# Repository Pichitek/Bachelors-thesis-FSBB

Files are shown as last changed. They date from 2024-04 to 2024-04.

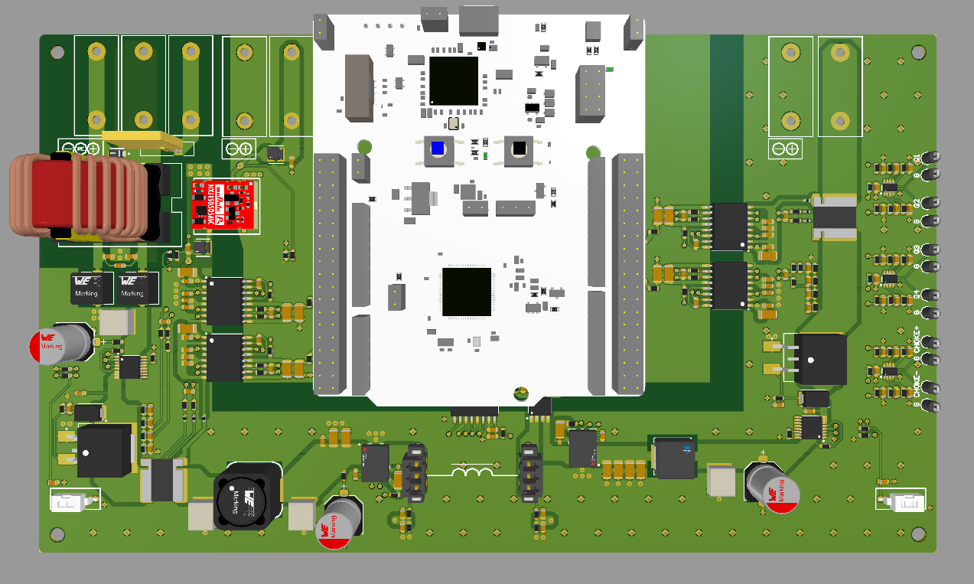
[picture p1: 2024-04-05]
images/altium/pcb_top.png

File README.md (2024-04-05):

# Laboratory model of Four Switch Buck-Boost converter

This project was part of my bachelors thesis at AGH University of Kraków. It contains schematic and PCB design made in Altium Designer 23, simulations of sensing ciruits, filters etc. made in LTSpice, control loop simulation conducted in Simulink and imprementation of control algorithm on STM32G4 microcontroller.

Due to lack of time, this project was finished in its simulation stage, although both schematic and PCB were reviewed by supervisor.

In this repository you can find:
* images folder with all screenshots, plots used while writing thesis
* sch_pcb folder with Altium Designer project
* sim folder with .asc files made in LTSpice
* src folder with control loop simulation, STMCubeIDE project and Jupyter notebook for calculations 
* .pdf's with schematic and thesis (as mentioned, it is written in polish)
* .ppt file which was presented during my defense (also in polish)

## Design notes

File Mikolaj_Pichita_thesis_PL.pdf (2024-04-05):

Akademia Górniczo-Hutnicza im. Stanisława Staszica w Krakowie

WYDZIAŁ INFORMATYKI, ELEKTRONIKI I TELEKOMUNIKACJI

## Projekt dyplomowy

## Model laboratoryjny przetwornicy typu „Buck-Boost” opartej na czterech kluczach tranzystorowych sterowanej cyfrowo Laboratory model of a digitally controlled buck-boost converter based on four transistor switches

Autor: | Mikołaj Pichita
Kierunek studiów: | Elektronika i Telekomunikacja
Opiekun pracy: | dr hab. inż. Cezary Worek, prof. AGH

Kraków, 2024

## Spis treści

SPIS TREŚCI | 3

SPIS TREŚCI | 4

## Wstęp

Przetwornice DC-DC Buck-Boost to uniwersalne urządzenia zapewniające dostarczenie napięcia zasilania z szerokiego zakresu. Łączy ona w sobie funkcjonalności przetwornicy Buck oraz Boost. Istnieje wiele różnych topologii dla tego typu przetwornic. Każda z nich posiada swoje zalety, ale również jest obarczona pewnego rodzaju wadami.
Dzięki cyfrowemu sterowaniu taka przetwornica jest w stanie zagwarantować sprawność na bardzo wysokim poziomie oraz stałe napięcie na wyjściu układu. W zaawansowanych systemach do sterowania nie są wykorzystywane powszechnie dostępne na rynku kontrolery. Bardzo często tworzony jest cały system sterowania na dedykowanym procesorze. Zapewnia to elastyczność, której standardowe kontrolery nie są w stanie zagwarantować. Pozwala stworzenie i kalibrację pętli sterowania dokładnie po zaprojektowany układ.

## Cel pracy

Celem pracy jest zaprojektowanie niskonapięciowej przetwornicy DC-DC typu Buck-Boost opartej na czterech kluczach tranzystorowych. Kontrola systemu powinna być zrealizowana poprzez mikrokontroler STM32G474 lub jego płytkę rozwojową. Układ został przygotowany jako model laboratoryjny do celów dydaktycznych.

1. Wprowadzenie do nieizolowanych przetwornic DC-DC | 5

## 1. Wprowadzenie do nieizolowanych przetwornic DC-DC

Niniejszy rozdział ma za zadanie opisać podstawowe funkcjonalności i właściwości nieizolowanych przetwornic DC-DC. Tematem pracy jest opracowanie modelu laboratoryjnego przetwornicy Buck-Boost. Z tego powodu skupiono się na objaśnieniu działania trzech podstawowych trybów działania przetwornicy: Buck, Boost, Buck-Boost oraz objaśnieniu cyfrowego sprzężenia zwrotnego, które zapewnia stabilność całego systemu, filtracji zaburzeń elektromagnetycznych oraz sposobów prowadzenia kluczowych, dla poprawnego działania przetwornicy, sygnałów.

### 1.1. Opis działania przetwornicy typu Buck

Cechą przetwornicy typu Buck jest zapewnienie napięcia wyjściowego układu, które będzie mniejsze od napięcia wejściowego. W najprostszej konfiguracji składa się ona z czterech elementów: elementu kluczującego, najczęściej tranzystora, elementu prostownika, w najprostszym przypadku diody, elementu magazynującego energię w polu magnetycznym oraz elementu filtrującego w postaci kondensatora. [1]

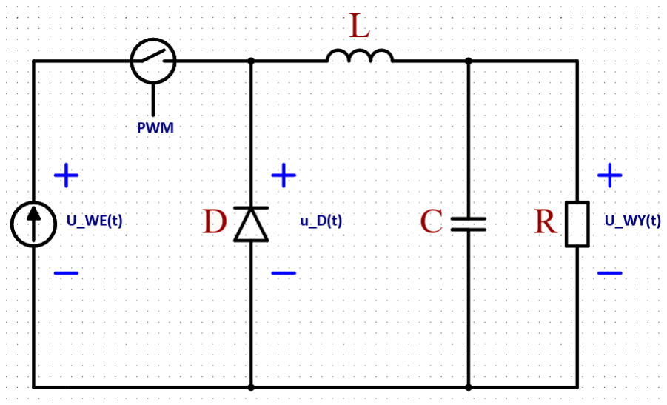
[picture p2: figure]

Rysunek 1. Przetwornica typu Buck

Klucz ma za zadanie obniżyć wartość napięcie wyjściowego przetwornicy poprzez jego włączanie i wyłączanie. Przez to, napięcie na diodzie będzie przypominać falę prostokątną ze współczynnikiem wypełnienia proporcjonalnym do stosunku czasów "włączenia"i "wyłączenia".

D =

tON
tON + tOF F

=

tON
TSW

(1.1)

Gdzie:

– D - współczynnik wypełnienia fali prostokątnej

– tON - czas włączenia tranzystora [s]

– tOF F - czas wyłączenia tranzystora [s]

– TSW - okres trwania jednego cyklu przełączania [s]

1. Wprowadzenie do nieizolowanych przetwornic DC-DC | 6

Aby otrzymać wartość stałą na wyjściu przetwornicy, należy posłużyć się filtrem dolnoprzepustowym. Taki filtr będzie spełniał rolę układu całkującego, tłumiąc składowe wysokoczęstotliwościowe przebiegów, przepuszczając głównie składową stałą przebiegu prostokątnego. W rezultacie można otrzymać wzór opisujący napięcie wyjściowe idealnego konwertera Buck.

VOUT = VIN · D | (1.2)

Gdzie:

– VOUT - napięcie wyjściowe przetwornicy [V]

– VIN - napięcie wejściowe przetwornicy [V]

### 1.2. Opis działania przetwornicy Boost

Przetwornica Boost zwiększa napięcie wyjściowe w stosunku do napięcia wejściowego. Urządzenie wykorzystuje takie same komponenty jak przetwornica Buck, ale zmieniając ich topologię, zapewnia inną funkcjonalność. [1]

Rysunek 2. Przetwornica typu Boost

Gdy klucz jest włączony, napięcie na elemencie indukcyjnym jest równe napięciu wejściowemu, a prąd elementu filtrującego jest równy prądowi obciążenia.

vL = VIN

iC = −

VOUT
R

(1.3)

Gdzie:

– vL - napięcie elementu indukcyjnego [V]

– iC - prąd elementu filtrującego [A]

W czasie, kiedy klucz jest wyłączony, element indukcyjny zmagazynował energię w polu magnetycznym. Ze względu na warunek zachowania ciągłości prądu, powoduje to zmianę napięcia na tym elemencie oraz zmianę prądu przepływającego przez element C.

1. Wprowadzenie do nieizolowanych przetwornic DC-DC | 7

vL = VIN − VOUT

iC = iL −

VOUT
R

(1.4)

Pozwala to wyprowadzić równanie na napięcie wyjściowe przetwornicy:

VOUT = VIN ·

1
1 − D

(1.5)

### 1.3. Opis działania przetwornicy Buck-Boost

Topologia Buck-Boost łączy funkcjonalność obu przetwornic. Taki układ potrafi wyprodukować napięcie wyjściowe, które może być zarówno mniejsze, jak i większe od napięcie wejściowego. Taka elastyczność jest często bardzo przydatna, gdy chcemy wykorzystać tę samą topologię do zasilania urządzeń o różnych napięciach zasilania. [1]

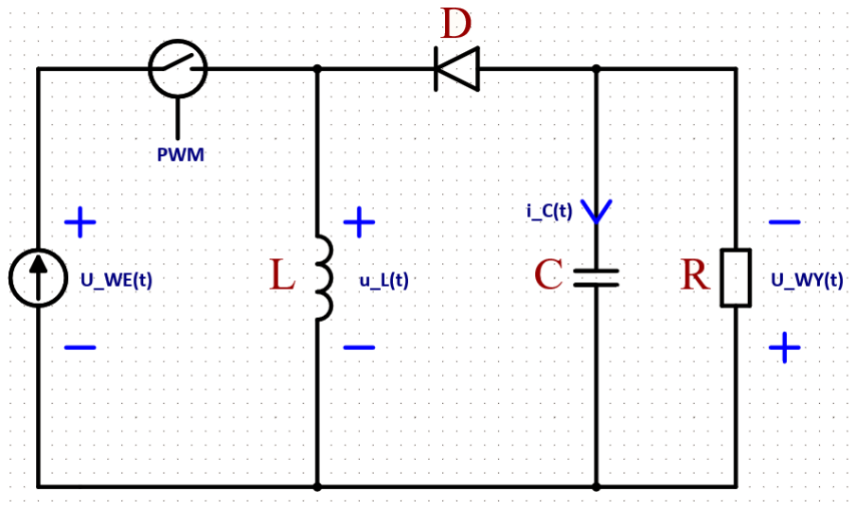
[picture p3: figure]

Rysunek 3. Odwracająca przetwornica typu Buck-Boost

VOUT = VIN ·

D
1 − D

(1.6)

Charakterystycznym elementem tej topologii jest odwrócone napięcie wyjściowe. Aby mogło być ono mierzone względem tego samego potencjału, należy posłużyć się inną topologią przetwornicy Buck-Boost, na przykład topologia SEPIC (single-ended primary-inductor converter) lub topologią opartą na czterech kluczach

tranzystorowych.

1. Wprowadzenie do nieizolowanych przetwornic DC-DC | 8

Rysunek 4. Przetwornica typu Buck-Boost na czterech kluczach

Wprowadzając do modelów przetwornic elementy pasożytnicze m.in. rezystancję szeregową induktora, rezystancję ON klucza, uzyskiwany jest model, który nie jest bezstratny. Parametr sprawności służy do opisywania stosunku mocy wejściowej i mocy wyjściowej przetwornicy, pokazując wpływ strat na jej pracę.

η =

POUT

PIN

(1.7)

Gdzie:

– η - sprawność

– POUT - moc wyjściowa przetwornicy [W]

– PIN - moc wejściowa przetwornicy [W]

### 1.4. Sprzężenie zwrotne przetwornicy DC-DC

Przetwornice impulsowe można opisać jako system składający się z parametrów: napięcia wejściowego UW E, prądu obciążenia (wyjściowego) IW Y i sygnału/ów PWM. Napięcie wyjściowe przetwornicy, będące równocześnie

sygnałem wyjściowym systemu, może być regulowane poprzez zmienianie parametrów wejściowych. Sprzężenia zwrotne w przetwornicach impulsowych są stosowane do zapewnienia stałego, znanego, napięcia wyjściowego. Wykorzystują one sensory prądów i napięć, regulując współczynnik wypełnienia sygnału sterującego klucze. [1]

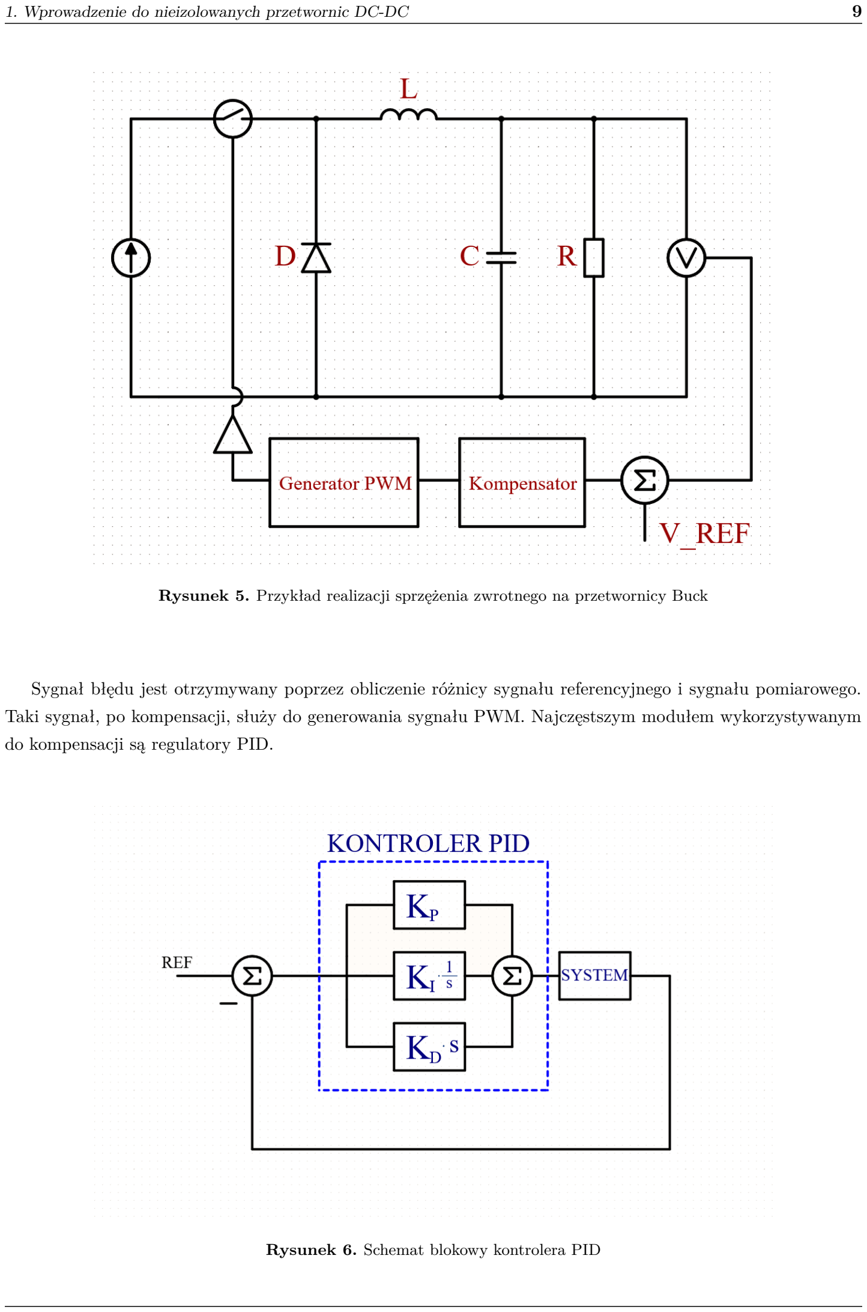
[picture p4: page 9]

1. Wprowadzenie do nieizolowanych przetwornic DC-DC | 9

Rysunek 5. Przykład realizacji sprzężenia zwrotnego na przetwornicy Buck

Sygnał błędu jest otrzymywany poprzez obliczenie różnicy sygnału referencyjnego i sygnału pomiarowego. Taki sygnał, po kompensacji, służy do generowania sygnału PWM. Najczęstszym modułem wykorzystywanym do kompensacji są regulatory PID.

Rysunek 6. Schemat blokowy kontrolera PID

1. Wprowadzenie do nieizolowanych przetwornic DC-DC | 10

Regulator PID (ang. Proportional-Integral-Derivative) jest odpowiedzialny za utrzymywanie stałej wartości

na wyjściu systemu, dynamicznie go regulując, wykorzystując sygnały referencyjne i wyjściowe. Wzmocnienie proporcjonalne KP , ma na celu zapewnienie zbieżności wartości referencyjnej i wyjściowej systemu. Taki regulator, wykorzystujący samo wzmocnienie KP , nie byłby w stanie zapewnić dokładniej zbieżności tych dwóch wartości z powodu błędu stanu ustalonego (ang. steady-state error). Do eliminacji tego błędu służy wzmocnie-

nie KI . Stosując operację całkowania, błąd steady-state, może być znacząco zredukowany, do tego stopnia, że regulatory PI są powszechnie stosowane w systemach sterowania. [8]

Rysunek 7. Typy odpowiedzi regulatora PID, [9]

Wzmocnienie KD, pomaga systemowi w jego tłumieniu, redukując przeregulowanie. Różne dostrojenie wartości KP , KI oraz KD będzie rezultować w różnych odpowiedziach czasowych systemu, minimalizując czas zbieżności lub przeregulowanie.

### 1.5. Filtracja zaburzeń elektromagnetycznych

Zaburzenia elektromagnetyczne to zjawisko objawiające się w powstawaniu zakłóceń w układzie elektronicznym. Wszystkie zakłócenia w systemie są wprowadzane do niego na dwa różne sposoby: poprzez przewodzenie lub poprzez promieniowanie. Oba typy mogą się demonstrować w postaci zakłóceń wspólnych (ang. common-mode) lub różnicowych (ang. differential-mode). Można prosto zdefiniować postaci tych zakłóceń na podstawie

przetwornic DC-DC.

W zasilaczach, naturalnym elementem przebiegów prądu są strome zbocza sygnałów. Takie szybkie zmiany, niosą za sobą dużą zawartość składowych harmonicznych, które mogą zakłócać pracę całego systemu. Taki typ zakłóceń można zdefiniować jako zakłócenia różnicowe. Zakłócenia pojawiają się w systemie na dodatnim biegunie oraz powracają poprzez ujemny biegun. [20]

1. Wprowadzenie do nieizolowanych przetwornic DC-DC | 11

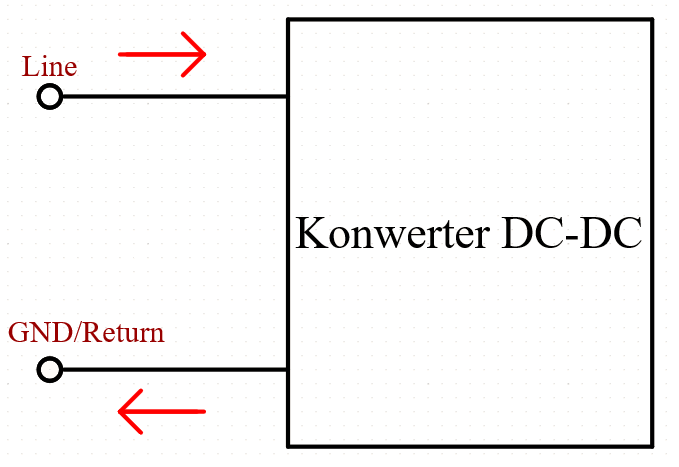
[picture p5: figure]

Rysunek 8. Zobrazowanie zakłóceń różnicowych

Do przedstawienia zakłóceń wspólnych można posłużyć się uproszczeniem. Polega ono na podłączeniu małej pojemności, rzędu kilkunastu pikofaradów, pomiędzy obudową zasilacza a potencjał PE (ang. Protective Earth).

Wszystkie zakłócenia wysokoczęstotliwościowe, nieważne czy pojawią się na biegunie dodatnim czy ujemnym, będą krążyć w systemie, co jest spowodowane sprzężeniem obudowy do PE.

Rysunek 9. Zobrazowanie zakłóceń wspólnych

Do filtracji zakłóceń EMI służą filtry EMI.

1. Wprowadzenie do nieizolowanych przetwornic DC-DC | 12

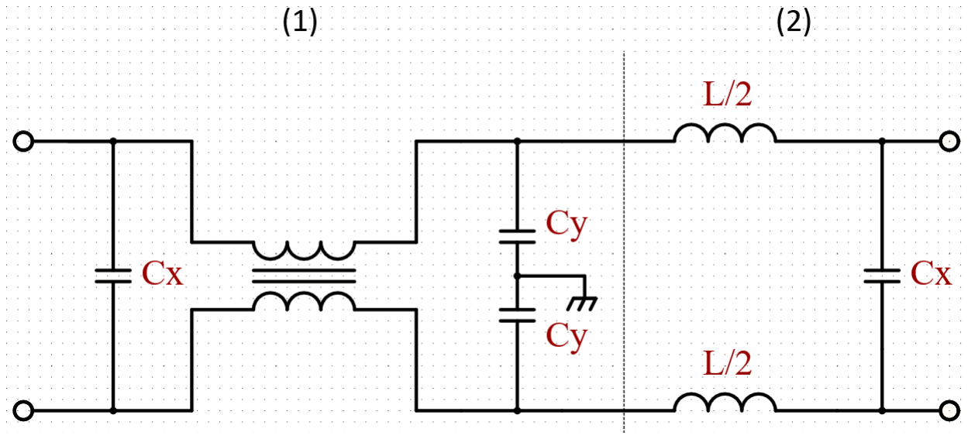
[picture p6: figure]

Rysunek 10. Filtr EMI

Filtr można podzielić na dwie części. Każda z nich jest odpowiedzialna za filtrację innego typu zakłóceń. Część różnicowa (2) to prosty filtr LC, dobrany tak, aby jego częstotliwość odcięcia zapewniała tłumienie zakłóceń powstających poprzez kluczowanie systemu. Część wspólna (1) jest zrealizowana przy pomocy dławika przeciwzakłóceniowego (ang. common-mode choke). Taki dławik, razem z odpowiednio dobranymi kondensato-

rami Cy, pozwala na odfiltrowanie wysokoczęstotliwościowych zakłóceń.
Aby uzyskać zadowalającą odpowiedź impulsową filtru, należy zadbać o jego poprawne tłumienie (ang damping). Damping zapewnia wyeliminowanie rezonansów pomiędzy elementami magnetycznymi a pojemnościo-

wymi, objawiających się w charakterystykach AC. Proces tłumienia polega na wprowadzeniu równolegle do układu dodatkowej gałęzi z pojemnością Cd oraz rezystancją Rd. Dobrym założeniem jest, aby wartość pojemności w gałęzi odpowiadającej za tłumienie, była od 5 do 10 razy większa od pojemności Cx. Aby zapewnić tłumienie krytyczne należy zadbać, aby dobroć układu była równa 1. [17]

Q =

1
R

·

r
L
C

(1.8)

Dzięki takiemu założeniu i wzorze [1.8] można poznać wartość rezystancji Rd.

Rd =

r
L
Cx | (1.9)

### 1.6. Techniki separacji i izolacji sygnałów w przetwornicach impulsowych

Częstą praktyką w przetwornicach DC-DC jest izolowanie toru mocy od części układu odpowiedzialnego za sterowanie. Jakość izolacji można podzielić na cztery klasy:

– izolacja funkcjonalna - najprostszy i najtańszy typ izolacji, w transformatorze izolującym nie występuje żadna warstwa izolująca jego uzwojenia, nie zapewnia ochrony przed porażeniem elektrycznym, służy głównie do przerywania na płycie PCB dużych pętli masy

– izolacja podstawowa - zapewnia ochronę przed porażeniem pod warunkiem, że warstwa materiału izolującego uzwojenia transformatora pozostała nienaruszona

– izolacja wspomagająca - porównując do izolacji podstawowej, dodawana jest kolejna warstwa materiału izolującego

1. Wprowadzenie do nieizolowanych przetwornic DC-DC | 13

– izolacja wzmocniona - oprócz izolacji uzwojeń, ten typ izolacji wymaga zachowania odpowiedniej odległości od elementów przewodzących

Problemem, z którym mierzą się przetwornice DC-DC, są zakłócenia pojawiające się na poligonie masy. Najprostszym sposobem na ochronę ważnych sygnałów, sterujących bramki tranzystorów, czy pomiarów prądu, napięcia, temperatury, jest zastosowanie pewnego rodzaju izolacji. Dzieląc potencjały odniesienia, redukowana jest szansa na zakłócenie sygnału wymaganego do pracy układu. [19]

2. Projekt przetwornicy | 14

## 2. Projekt przetwornicy

W poniższym rozdziale zostanie szczegółowo omówiony proces projektowania przetwornicy Buck-Boost. Zostaną zaprezentowane bloki funkcjonalne przetwornicy, fragmenty schematu, uzasadnienia wyboru komponentów, a na sam koniec omówiony zostanie projekt PCB. Schematy i płytkę PCB zaprojektowano korzystając z programu Altium Designer.

### 2.1. Założenia projektowe

Aby rozpocząć projektowanie przetwornicy, wymagane było zdefiniowanie pewnych założeń. Pozwoliło to na wybór odpowiednich komponentów i zapewniło punkt startowy dla projektu.

Tabela 1. Założenie projektowe przetwornicy Buck-Boost

Napięcie wejściowe | 5 ÷ 24 [V]
Napięcie wyjściowe | 3.3 ÷ 24 [V]
Moc maksymalna | ∼ 50 [W]
Częstotliwość przełączania | 100 ÷ 300 [kHz]
Platforma bazowa | Nucleo G474RE [13]

Dodatkowe założenia:

– Zalecane użycie półmostka LMG5200 [10]

– filtr EMI na wejściu przetwornicy

– pomiar prądu dławika ACS730KLCTR-20AB-T [3]

– zasilanie logiki +5V

### 2.2. Opis wybranej topologii

Do realizacji projektu wykorzystano topologię przetwornicy Buck-Boost opartą na czterech kluczach tranzystorowych (rysunek 4). Ta konfiguracja charakteryzuje się dużą sprawność systemu, rzędu 95%, oraz jest w

stanie zapewnić wysoką moc wyjściową. Cztery klucze tranzystorowe, w przeciwieństwie do przetwornicy Buck-Boost opisywanej w sekcji 1.3, umożliwiają pracę przetwornicy w trzech trybach: Buck, Boost oraz w trybie mieszanym Buck-Boost.

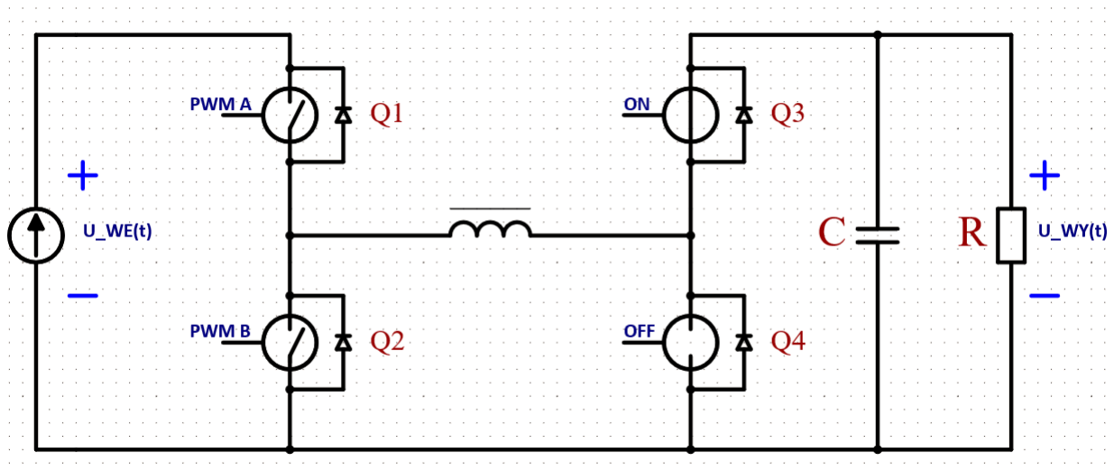
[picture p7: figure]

Rysunek 11. Przetwornica Buck-Boost w trybie Buck

2. Projekt przetwornicy | 15

Tryb Buck zostaje uruchomiony, gdy zadane napięcie wyjściowe UW Y jest mniejsze od napięcia wejściowego UW E przetwornicy. Tranzystory Q1 oraz Q2 są sterowane komplementarnym sygnałem PWM. Tranzystor Q3 oraz Q4 nie są przełączane w tym trybie pracy, do poprawnego działania wymagane jest, aby tranzystor Q3 był włączony, a Q4 wyłączony. Aby uniknąć przypadkowego zwarcia, ważna jest konfiguracja czasu martwego (ang. deadtime), czyli odstępu w czasie między zboczami sygnałów sterujących. W tym trybie przetwornica działa

tak jak opisano w sekcji 1.1.

Rysunek 12. Przetwornica Buck-Boost w trybie Boost

Tryb Boost zostaje uruchomiony, gdy zadane napięcie wyjściowe UW Y jest większe od napięcia wejściowego UW E. Tym razem tranzystory Q1 (przewodzi) oraz Q2 (nie przewodzi) nie uczestniczą w kluczowaniu, natomiast

tranzystory Q3 i Q4 są sterowane komplementarnym sygnłem PWM. Tak kontrolowany układ zachowuje się jak opisano w sekcji 1.2.

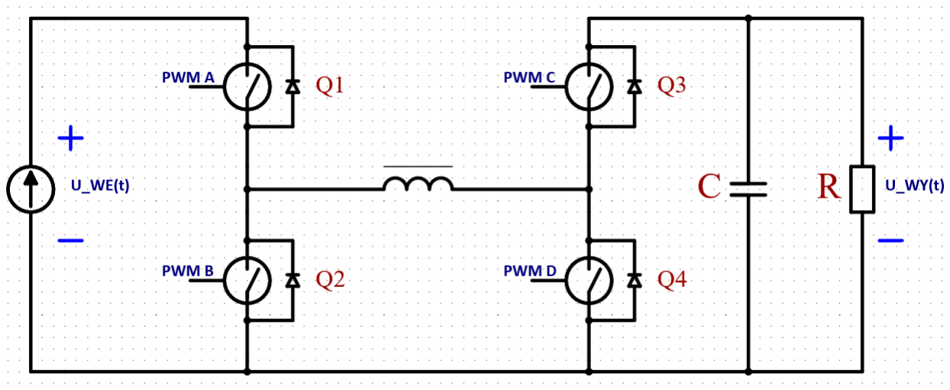
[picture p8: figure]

Rysunek 13. Przetwornica Buck-Boost w trybie mieszanym

Gdy zadane napięcie wyjściowe UW Y jest bliskie napięciu wejściowemu UW E, przetwornica wchodzi w tryb mieszany. Ma on za zadanie stanowić płynne przejście między trybami pracy Buck i Boost. W tym trybie, kluczowane są wszystkie tranzystory, zapewniając obniżenie napięcia w sekcji Buck oraz jego podwyższenie w sekcji Boost, tak, aby napięcie wyjściowe miało wartość bliską do wartości napięcia wejściowego. Podobnie jak w przypadku innych topologii można wyprowadzić wzór opisujący stosunek napięcie wyjściowego do napięcia wejściowego, co umożliwi na wyrażenie UW Y przy pomocy współczynników wypełnienia oraz UW E.

VOUT = VIN ·

D1
1 − D2

(2.1)

Gdzie:

– D1 - współczynnik wypełnienia komplementarnego sygnału PWM sterującego częścią Buck

2. Projekt przetwornicy | 16

– D2 - współczynnik wypełnienia komplementarnego sygnału PWM sterującego częścią Boost

Za elementy kluczujące w tym projekcie posłużą dwa półmostki, z wbudowanymi sterownikami bramek, firmy Texas Instruments, LMG5200 [10]. Wykorzystują one tranzystory FET wykonane w technologii GaN. Te

moduły cechują się bardzo niską pojemnością wejściową oraz polem lutowniczym minimalizującym elementy pasożytnicze.

### 2.3. Schemat blokowy

Aby uprościć proces projektowania przetwornicy, cały system podzielono na bloki funkcyjne. Na schemacie zostały wyróżnione bloki:

– Filtr EMI: zawierający prosty filtr zakłóceń elektromagnetycznych

– Układ protekcyjny: układ zabezpieczający przed nadmiernym natężeniem prądu oraz zbyt wysokim napięciem

– Pomiar napięcia DC: zrealizowany przy pomocy wysokoimpendancyjnego, skompensowanego, dzielnika napięcia

– Pomiar prądu DC: zrealizowany przy pomocy rezystora typu shunt

– Filtr wejściowy: filtr w topologii PI, odpowiedzialny za tłumienie zakłóceń wynikających z przełączania tranzystorów

– Przetwornica: tranzystory w konfiguracji pełnego mostka

– Pomiar prądu AC: zrealizowany przy pomocy czujnika Halla, odpowiedzialny za pomiar prądu dławika

– Filtr wyjściowy: filtr redukujący tętnienia prądu i napięcia na wyjściu przetwornicy

– Izolator sygnałów PWM: układ wymagany do zapewnienia izolacji pomiędzy częścią sterowania a częścią mocy

– Izolowany układ zasilający: zasilanie logiki po stronie izolowanej

– Mikrokontroler: sterowanie, obsługa ADC oraz generowanie sygnałów PWM

2. Projekt przetwornicy | 17

Rysunek 14. Schemat blokowy przetwornicy Buck-Boost

### 2.4. Dobór elementów magnetycznych

Elementy magnetyczne w przetwornicach DC-DC to kluczowe elementy, a ich dobór to problem, z którym należy się zmierzyć w trakcie projektowania. Głównym czynnikiem ograniczającym wybór, i niosącym ze sobą liczne konsekwencje przy dobieraniu dławika w przetwornicy, to częstotliwość pracy systemu. Im ta częstotliwość jest większa, tym mniejsza wartość indukcyjności będzie wymagana do poprawnego działania przetwornicy. Zmiana induktancji będzie wprowadzać ograniczenie czysto mechaniczne. Im większa induktancja dławika, tym fizycznie on będzie musiał być większy. Mając na uwadze, że założona częstotliwość przełączania ma wynosić od 100kHz do 300kHz, wymagane będzie, w późniejszym etapie projektowania, zapewnienie pewnego rodzaju modularności, pozwalającej na zmianę dławika, w zależności od częstotliwości pracy. Do obliczenia minimalnej wartości induktancji elementu magnetycznego posłużono się wzorami 2.2 oraz 2.3 [7].

Minimalna wartość induktancji dla przetwornicy typu Buck:

L > UW Y · (UW Emax − UW Y )

Kind · fSW · UW Emax · IW Y

(2.2)

Minimalna wartość induktancji dla przetwornicy typu Boost:

L > U

2
W E · (UW Y − UW Emax)

Kind · fSW · U

2
W Y · IW Y

(2.3)

Gdzie:

2. Projekt przetwornicy | 18

– UW Y - napięcie wyjściowe przetwornicy

– UW E - napięcie wejściowe przetwornicy

– Kind - współczynnik reprezentujący tętnienia prądu dławika, założono wartość 30%

– fSW - częstotliwość przełączania

– IW Y - prąd wyjściowy przetwornicy

Za pomocą skryptu, napisanego w języku Python, obliczono minimalne wartości indukcyjności dławików dla obu typów pracy pod pełnym obciążeniem (maksymalna moc wyjściowa). Wyniki zawarto w tabeli poniżej.

Tabela 2. Minimalne wartości indukcyjności dławika

fSW | LBUCKmin | LBOOSTmin
100kHz | 56.89µH | 13.94µH
150kHz | 37.92µH | 8.79µH
200kHz | 28.44µH | 6.59µH
250kHz | 22.75µH | 5.27µH
300kHz | 18.96µH | 4.39µH

Wartości LBOOSTmin zostały odrzucone, ponieważ te wartości są znacząco niższe niż LBOOSTmin, a układ musi być przygotowany na pracę w obu trybach.

W projekcie użyto induktorów mocy firmy Pulse Electronics [15]. Wykorzystanie komponentów z jednej serii

pozwala na wykorzystanie w projekcie jednego pola lutowniczego, mimo tego, że poszczególne induktory będą miały inną wartość induktancji.

Tabela 3. Wybrane induktory

Nazwa | Indukcyjność | DCR | ISAT @25°C
PA2050.583NL | 57.8µH | 34.5mΩ | 6.2 A
PA2050.393NL | 38.9µH | 18.8mΩ | 6.3 A
PA2050.313NL | 31.4µH | 20.2mΩ | 8.4 A
PA2050.233NL | 23.0µH | 13.7mΩ | 9.8 A
PA2050.193NL | 19.4µH | 12.6mΩ | 11 A

### 2.5. Zasilanie pomocnicze i izolacja sygnałów

W projekcie zdecydowano się na odizolowanie części sterowania od toru mocy. Wiąże się to z korzystaniem elementów gwarantujących zachowanie izolacji, bez zaburzania funkcjonalności. Część sterująca jest zasilania zewnętrznie, tj. przy pomocy zasilacza laboratoryjnego. Aby układy po stronie toru mocy (po stronie izolowanej)

miały zapewnione zasilanie, niezależnie od napięcia wejściowego przetwornicy, posłużono się izolowaną przetwornicą NXJ1S0505MC [14]. Zapewnia ona moc 1W, co daje prąd wyjściowy przetwornicy 200mA przy napięciu

wyjściowym +5VDC. Jest to wystarczająca wartość do zasilenia wszystkich układów po stronie izolowanej.

2. Projekt przetwornicy | 19

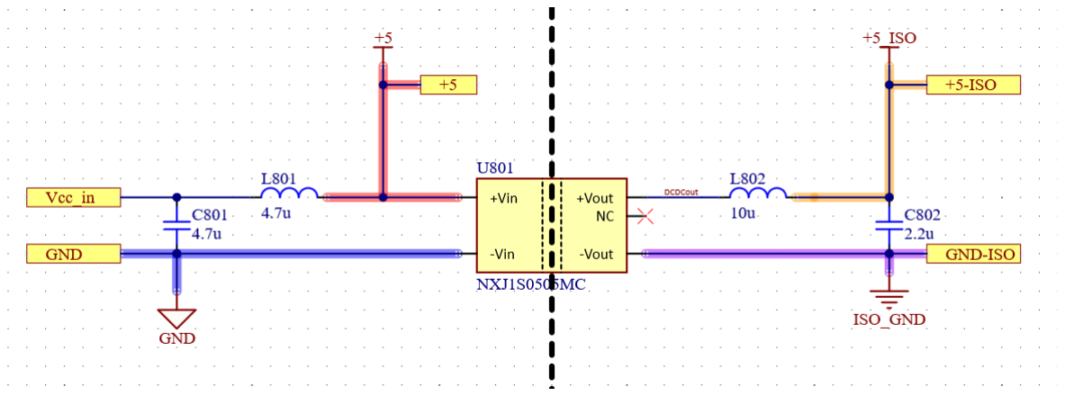
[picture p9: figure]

Rysunek 15. Fragment schematu zawierający izolowany zasilacz NXJ1S0505MC

Mając na uwadze to, że sygnały mikrokontroler, generujący sygnały PWM i półmostki LMG5200, nie będą znajdować się na tym samym potencjale masy, wymagane będzie użycie izolatora sygnałów. W projekcie wykorzystano izolator cyfrowy firmy Analog Devices ADuM340E [4]. Jest to izolator z dużą przepustowością, który

pozwoli na niezawodną transmisję wygenerowanych sygnałów PWM.

Rysunek 16. Fragment schematu zawierający cyfrowy izolator ADuM340E

### 2.6. Układ zabezpieczających

Aby zapewnić pracę układu w zdefiniowanych parametrach, sekcja 2.1, i ochronę przed pojawieniem się nadmiernego napięcia lub natężenia prądu, został zaprojektowany układ zabezpieczający. Składa się on z części chroniącej przed zbyt dużym natężeniem prądu (ang. overcurrent) oraz z części chroniącej przed zbyt wysokim napięciem (ang. overvoltage).
Do ochrony overcurrent wykorzystano High-Side switch firmy Texas Instruments TPS1HB16A-Q1 [21].

Dzięki możliwości ustawienia dokładnego progu, po którego przekroczeniu urządzenie otwiera obwód, efektywnie zatrzymując przepływ prądu, możliwe było precyzyjne dostosowanie tego układu do pracy. Próg, powodujący otwarcie klucza, został ustawiony na wartość 5A.

2. Projekt przetwornicy | 20

Do ochrony przed overvoltage wykorzystano klasyczny układ z tyrystorem (ang. crowbar).

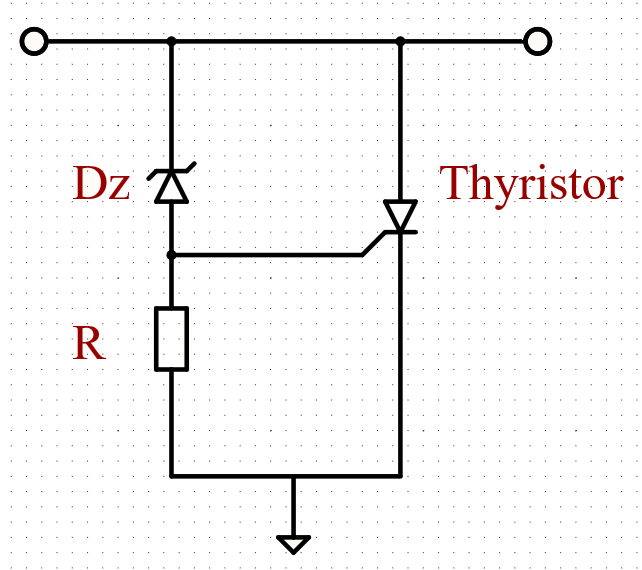
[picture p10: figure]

Rysunek 17. Schemat ideowy układu crowbar

Gdy zostanie przekroczone napięcie Zenera diody Dz, zacznie ona przewodzić, powodując spadek napięcia na rezystorze R. Przez to, nastąpi wysterowanie tyrystora, zwierając wyjście układu do potencjału masy.

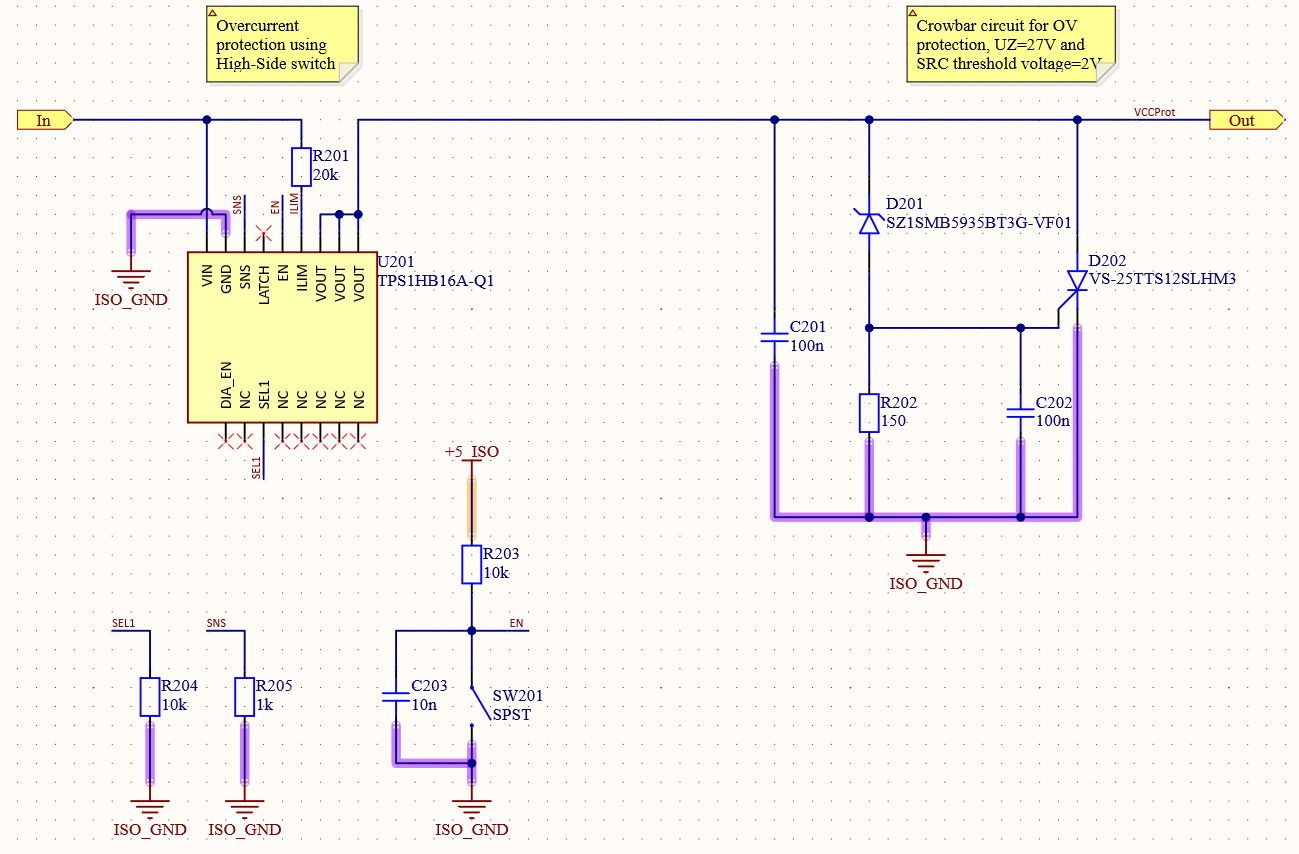
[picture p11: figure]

Rysunek 18. Fragment schematu zawierający układ protekcyjny

2. Projekt przetwornicy | 21

### 2.7. Opis układów pomiarowych

Do zaimplementowania sprzężenia zwrotnego, w projekcie wymagane jest przeprowadzenie pomiarów bezpośrednio na płytce PCB. Następnie, dane są przekazywane do mikrokontrolera, gdzie realizowany jest algorytm sterowania systemu. W tej sekcji zostaną sposoby, w jakie mierzone są prądy i napięcia na płytce PCB.

### 2.7.1. Pomiary prądów przy pomocy rezystora typu shunt

Do pomiary prądów stałych, tj. prądu wejściowego i wyjściowego, wykorzystano pomiar napięcie na rezystorze typu shunt. Są to rezystory o bardzo małej wartości rezystancji, rzędu pojedynczych miliohmów lub kilkuset mikroohmów.

Rysunek 19. Schemat ideowy układu pomiaru prądu z rezystorem typu shunt

Prąd, który płynie przez rezystor R, powoduje, że odkłada się na nim napięcie. To napięcie jest następnie wzmacniane przez wzmacniacz różnicowy. Napięcie wyjściowe tego układu jest proporcjonalne do prądu płynącego przez rezystor R i można je opisać wzorem:

UW Y = U · G ⇒ I =

UW Y
G · R

(2.4)

Gdzie:

– U - spadek napięcia na shuncie [V]

– I - prąd płynący przez shunt [A]

– G - wzmocnienie [V/V]

Do realizacji tego układu w projekcie posłużono się wzmacniaczem izolowanym z rodziny AMC od firmy Texas Instruments, [5]. Wzmacniacz ten charakteryzuje się niskim napięciem wejściowym ±50mV , co umożliwia

na zminimalizowanie strat mocy przy pomiarze, oraz wbudowaną przetwornicą DC-DC, zasilającą układ po stronie wtórnej. Ten układ został wykorzystany jedynie do pomiarów DC, ponieważ wzmacniacze izolowane posiadają bardzo ograniczone pasmo przenoszenia. Układ AMC3302 posiada pasmo przenoszenia około 300kHz, co jest niewystarczającą wartością do pomiaru prądów zmiennych o częstotliwości od 100kHz do 300kHz.

2. Projekt przetwornicy | 22

Rysunek 20. Fragment schematu zawierający układu pomiaru prądu z rezystorem typu

shunt

Wyjście wzmacniacza jest również różnicowe. Dzięki temu na płytce PCB poprowadzona została para różnicowa prosto z wyjścia wzmacniacza do konwertera analogowo-cyfrowego.

### 2.7.2. Pomiar prądu cewki przy pomocy czujników Halla

Do pomiaru prądów zmiennych, popularnym rozwiązaniem są układy scalone wykorzystujące sensory Halla. Poprzez dużą dynamikę, te układy, bezproblemowo radzą sobie z pomiarem prądów o dużych częstotliwościach. W projekcie wykorzystano układ firmy Allegro, ACS730 [3]. Jest to izolowany sensor prądu, o paśmie przeno-

szenia 1MHz oraz bardzo niskiej rezystancji 1.2mΩ.

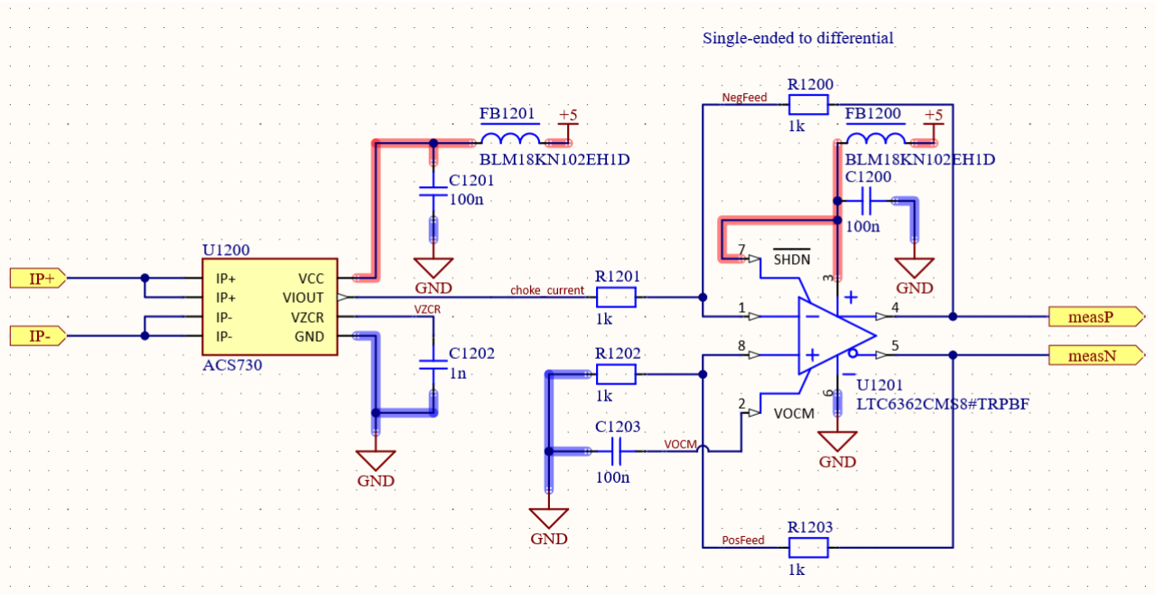
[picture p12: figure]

Rysunek 21. Fragment schematu zawierający sensor prądu ACS730

Ponieważ wartość wyjściowa układu ACS730 zwracana jest względem potencjału masy (ang. single-ended), poddano ten sygnał konwersji wykorzystując sterownik przetworników ADC LTC6362, [12]. Dzięki temu uzy-

skano sygnał w postaci pary różnicowej, zamiast sygnału single-ended.

2. Projekt przetwornicy | 23

### 2.7.3. Pomiary napięć

Do pomiaru napięć DC wykorzystano wysokoimpedancyjny dzielnik napięcia. Ogranicza to pobierany przez układ prąd, redukując straty mocy.

Rysunek 22. Schemat ideowy pomiaru napięcia na dzielniku

Pozwala to na uzyskanie wartości wyjściowej układu, która jest proporcjonalna do mierzonego napięcia.

U2 =

U · R2
R1 + R2 + R3

(2.5)

UW Y = U2 · G ⇒ U =

UW Y · R1 + R2 + R3
G · R2

(2.6)

Pomiar napięć DC, podobnie jak pomiar prądów DC, został zrealizowany wykorzystując wzmacniacz izolowany firmy Texas Instruments z rodziny AMC, AMC3330 [6]. Różni się on od AMC3302 maksymalnym napięciem wejściowym które wynosi ±1V .

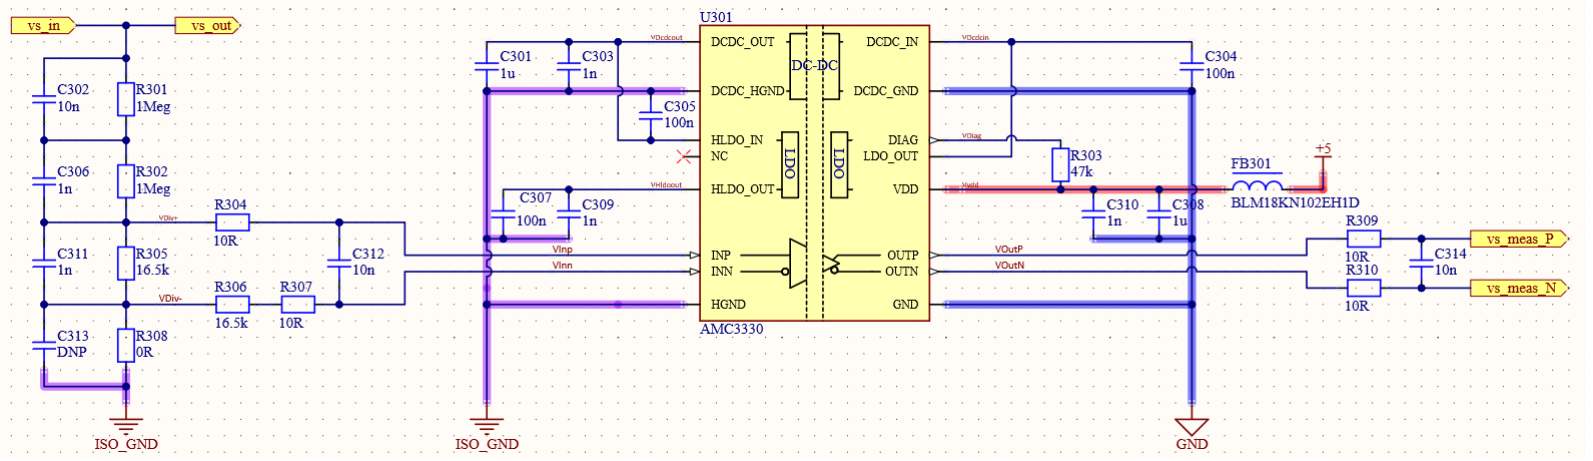
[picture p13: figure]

Rysunek 23. Fragment schematu zawierający układ pomiaru napięcia

2. Projekt przetwornicy | 24

### 2.7.4. Testowe punkty pomiarowe

Projekt ma służyć jako platforma dydaktyczna, dlatego postanowiono umieścić łącznie 6 punktów pomiarowych, umożliwiające obserwowanie, za pomocą oscyloskopu, kluczowych dla pracy przetwornicy sygnałów. Do tego celu wykorzystano szerokopasmowy wzmacniacz operacyjny firmy Analog Devices LTC6262 [11]. Pasmo

przenoszenia tego wzmacniacza wynosi 30MHz, co zapewni możliwość zaobserwowania dokładnych przebiegów na stanowisku pomiarowym. Wzmacniacz został skonfigurowany jako aktywny filtr dolnoprzepustowy, trzeciego rzędu, Sallen-Key, o częstotliwości odcięcia równej 30MHz.

Rysunek 24. Fragment schematu zawierający układ punktu pomiarowego

### 2.8. Filtracja torów zasilania DC

Pasywne filtry to rzecz spotykana, w każdej przetwornicy DC-DC, w tym podrozdziale zostanie omówiony proces projektowania filtrów EMI, wejściowych oraz wyjściowych.

### 2.8.1. Filtr EMI

Filtracja zaburzeń elektromagnetycznych, tak jak opisano w sekcji 1.5, jest kluczowym aspektem przy projektowaniu przetwornic DC-DC. Poprzez podział filtra na sekcję wspólną oraz różnicową, tak jak na rysunku 10, można w łatwy sposób wybrać dławik przeciwzakłóceniowy oraz oszacować wartości komponentów L, Cx oraz Cy.

Przy projektowaniu części różnicowej należy, za częstotliwość odcięcia, wybrać częstotliwość 10 razy mniejszą od częstotliwości przełączania systemu. Ponieważ przetwornica ma pracować na częstotliwości od 100kHz do 300kHz, za częstotliwość odcięcia obrano 10kHz.

fc =

1
2 · π ·

√
L · C

(2.7)

Przy założeniu, że induktancja filtru wynosi 10µH, można obliczyć pojemność Cx, która będzie wynosić 15µF. Łączną induktancję L należy podzielić na dwa mniejsze induktory L/2 i umieścić je odpowiednio na torze

dodatnim oraz ujemnym.

2. Projekt przetwornicy | 25

Do części wspólnej został wybrany dławik firmy Würth Elektronik [2] o indukcyjności 2.2mH. Dla konwer-

terów DC-DC dobrym założeniem jest, że zakłócenia common-mode pojawiają się w okolicach częstotliwości 7.5MHz. Dla tej częstotliwości oczekiwane jest już tłumienie na poziomie co najmniej 80dB, co daje w rezultacie częstotliwość odcięcia równą 75kHz. Dzięki temu można obliczyć, korzystając ponownie ze wzoru 2.7, wartość pojemności Cy, która będzie wynosić 2.2nF.
Wartości kondensatora oraz rezystora tłumiącego zostały obrane zgodnie z opisem znajdującym się w sekcji 1.5 i wynoszą Cd = 82µF, Rd = 1Ω. Warto nadmienić, że w odróżnieniu od większości kondensatorów wykorzystywanych w projekcie, kondensator Cd jest kondensatorem elektrolitycznym aluminiowym. Jest to spowodowane dużą rezystancją szeregową ESR ((ang. equivalent series resistance)), działającą często jako rezystor Rd oraz

dostępnością znacznie większych pojemności.

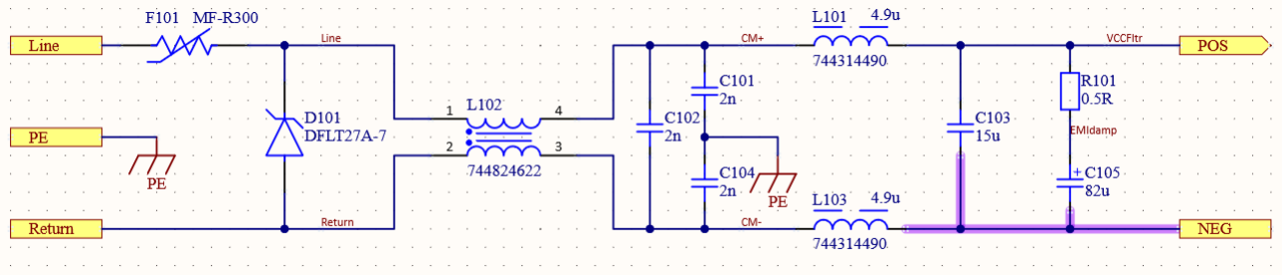
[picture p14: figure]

Rysunek 25. Fragment schematu zawierający układ filtru EMI

Dodatkowo w projekcie filtru wykorzystano diodę TVS oraz reprogramowalny bezpiecznik.

### 2.8.2. Filtr wejściowy

Filtr wejściowy przetwornicy ma za zadanie wyeliminować zakłócenia wynikające z przełączania tranzystorów oraz zakłócenia pochodzące ze źródła napięcia dostarczającego energię do systemu. Do realizacji takiego zadania wybrano filtr typu PI.

Rysunek 26. Filtr typu Pi

Przy projektowaniu filtru należy zwrócić uwagę na parametr SRF (ang. self resonant frequency) cewki L i kondensatora C1 (rysunek 26), dodatkowo mając na uwadze, aby SRF cewki była mniejsza od SRF kondensa-

tora. Częstotliwość przełączania znajduje się w obrębie od 100kHz do 300kHz, co oznacza, że rdzeń cewki nie jest krytycznym czynnikiem przy wyborze tego elementu.

2. Projekt przetwornicy | 26

Jako częstotliwość odcięcia wybrano wartość 10 razy mniejszą od minimalnej częstotliwości przełączania tranzystorów, co daje fc = 10kHz.

Zakładając wartość indukcyjności cewki L = 15µH, na podstawie wzoru 2.7, można obliczyć wartość pojemności kondensatora C1, która będzie się równać 16.87µF. Jako rzeczywistą wartość tego kondensatora wybrano 18µF. Zmienia to częstotliwość odcięcia, która będzie wynosić nie 10kHz, a 12kHz. Ta zmiana nie powinna znacząco wpłynąć na efektywność działania filtru.

Przy wyborze kondensatora C2 kluczową rolę odgrywa parametr SRF. Wybrany komponent powinien mieć częstotliwość rezonansową równą częstotliwości przełączania tranzystorów. Ze względu na dosyć niską częstotliwość przełączania, nie udało się wybrać kondensatora z SRF w tych okolicach. Wybrany element posiada częstotliwość rezonansową dla częstotliwości 500kHz, a dla częstotliwości przełączania wykazuję się niską impedancją, na poziomie około 15mΩ.

W konfiguracji przedstawionej na rysunku 26, dla częstotliwości odcięcia, filtr będzie znacząco wzmacniać sygnał zamiast go tłumić. To zjawisko można wyeliminować stosując tłumienie filtru.

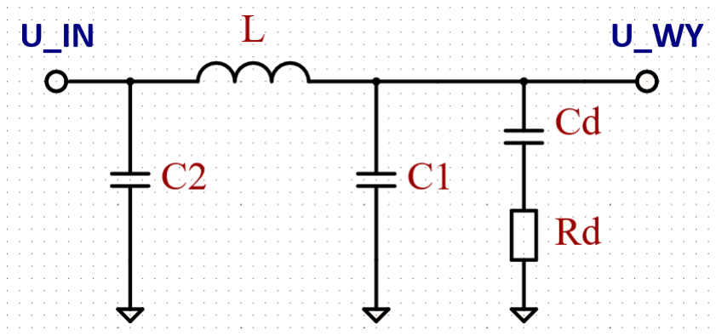
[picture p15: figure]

Rysunek 27. Filtr EMI typi Pi z dołączonymi elementami Cd i Rd

Q =

1
Rd

s
Lf
Cf1

(2.8)

Przy założeniu, że dobroć filtru ma być równa 1 można obliczyć wartość rezystancji Rd na podstawie wzoru
2.8. Aby zniwelować efekt rezonansu, dobrano komponenty o wartościach: Cd = 82µF i Rd = 1Ω. Jako kondensator Cd, ponownie został wybrany kondensator aluminiowy. ESR połączone szeregowo razem z rezystancją Rd = 0.5Ω dają rezystancję zastępczą równą około 1Ω.

2. Projekt przetwornicy | 27

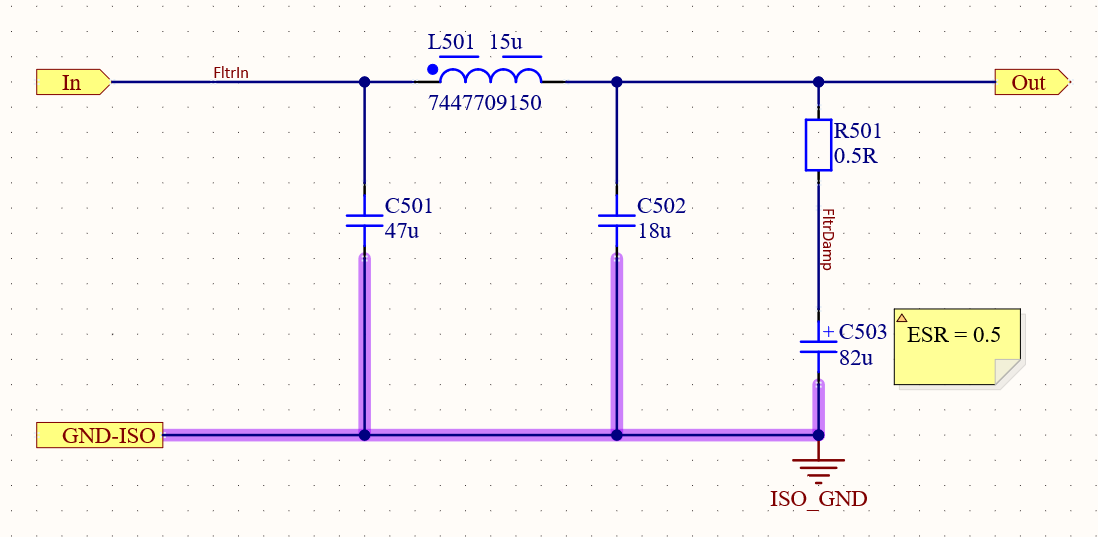
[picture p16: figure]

Rysunek 28. Fragment schematu zawierający układ filtru wejściowego

### 2.8.3. Filtr wyjściowy

Zadaniem filtra wyjściowego jest redukcja zakłóceń spowodowanych przełączaniem oraz ograniczenie tętnień. Ponownie jako topologię filtra wybrano topologię PI, rysunek 26, pozwala to na uzyskanie jasno zdefiniowanej pojemności wyjściowej przetwornicy oraz wyeliminowanie zakłóceń, wykorzystując filtr LC. Za pojemność wyjściową służy bank kondensatorów. Są to 4 kondensatory MLCC, każdy o pojemności 4.7µF, połączone równolegle, co łącznie daje pojemność 18.8µF. Wartości komponentów zawartych w filtrze LC obliczono identycznie, jak w sekcji 2.8.2. Założono wartość indukcyjności L, tym razem 8.2µH, a na podstawie wzoru 2.7 obliczono pojemność. Na sam koniec zadbano o prawidłowe tłumienie filtru, w tym celu posłużono się kondensatorem aluminiowym.

Rysunek 29. Fragment schematu zawierający układ filtru wyjściowego

2. Projekt przetwornicy | 28

### 2.9. Projekt PCB

W ramach projektu zaprjektowano płytkę PCB. Ze względu na to, że płytka ma zostać przeznaczona do celów dydaktycznych, zminimalizowanie rozmiarów płytki nie było priorytetem. Głównym celem było przejrzyste rozmieszczenie bloków funkcyjnych na płycie, tak, aby patrząc na schemat, można było zidentyfikować komponent na płytce.

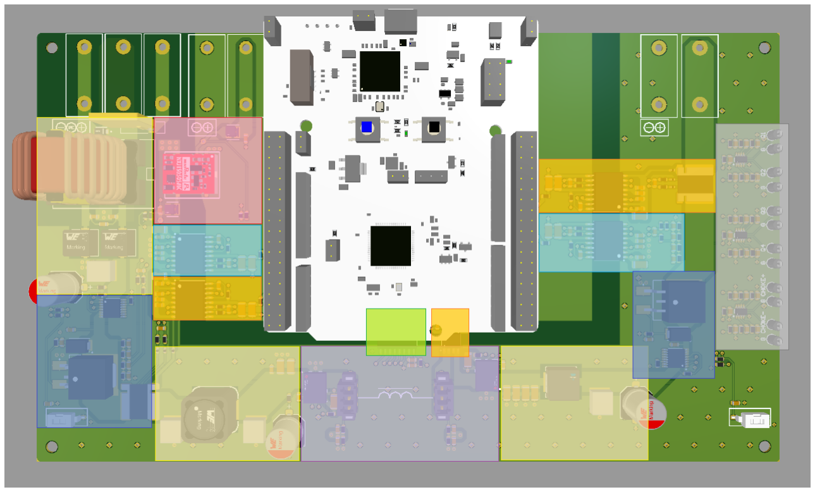
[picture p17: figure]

Rysunek 30. Widok płytki PCB z zaznaczonymi blokami funkcyjnymi

Gdzie (idąc od strony lewej do prawej):

– sekcja żółta - filtry: EMI, wejściowy oraz wyjściowy

– sekcja granatowa - układ zabezpieczający

– sekcja czerwona - izolowany układ zasilania

– sekcja jasno-niebieska - izolowany pomiar napięcia

– sekcja pomarańczowa - izolowany pomiar prądu

– sekcja fioletowa - przetwornica

– sekcja zielona - izolator sygnałów PWM

– sekcja szara - punkty testowe

Płytka została zrealizowana w technologii czterowarstwowej.

2. Projekt przetwornicy | 29

W miejscu elementu indukcyjnego znajdują się dwa złącza. Jest to związane z wymogiem zapewnienia różnych wartości indukcyjności dla różnych częstotliwości pracy układu. Wybór wartości cewek został omówiony w sekcji 2.4.

Rysunek 31. Stackup płytki czterowarstwowej, [16]

Na warstwie pierwszej (Top Layer) zostały umieszczone wszystkie komponenty oraz poprowadzony został tor mocy. Po warstwie drugiej (Midlayer 1) zostały poprowadzone sygnały zasilające układy na płytce. Warstwa trzecia (Midlayer 2) zawierała sygnały wrażliwe na zakłócenie (pomiary, sygnały poprowadzone to punktów pomiarowych). Na czwartej warstwie (Bottom layer) znajduje się poligon masy. Dodatkowo, na wszystkich

warstwach został wylany potencjał masy oraz płytka została połączona przelotkami, w celu zminimalizowania powstających pętli masy. Pod elementami indukcyjnymi, znajdującymi się bezpośrednio na płytce, umieszczono wycięcie (ang. cutout) w rozlanym poligonie.

## 3. Model symulacyjny przetwornicy typu Buck-Boost

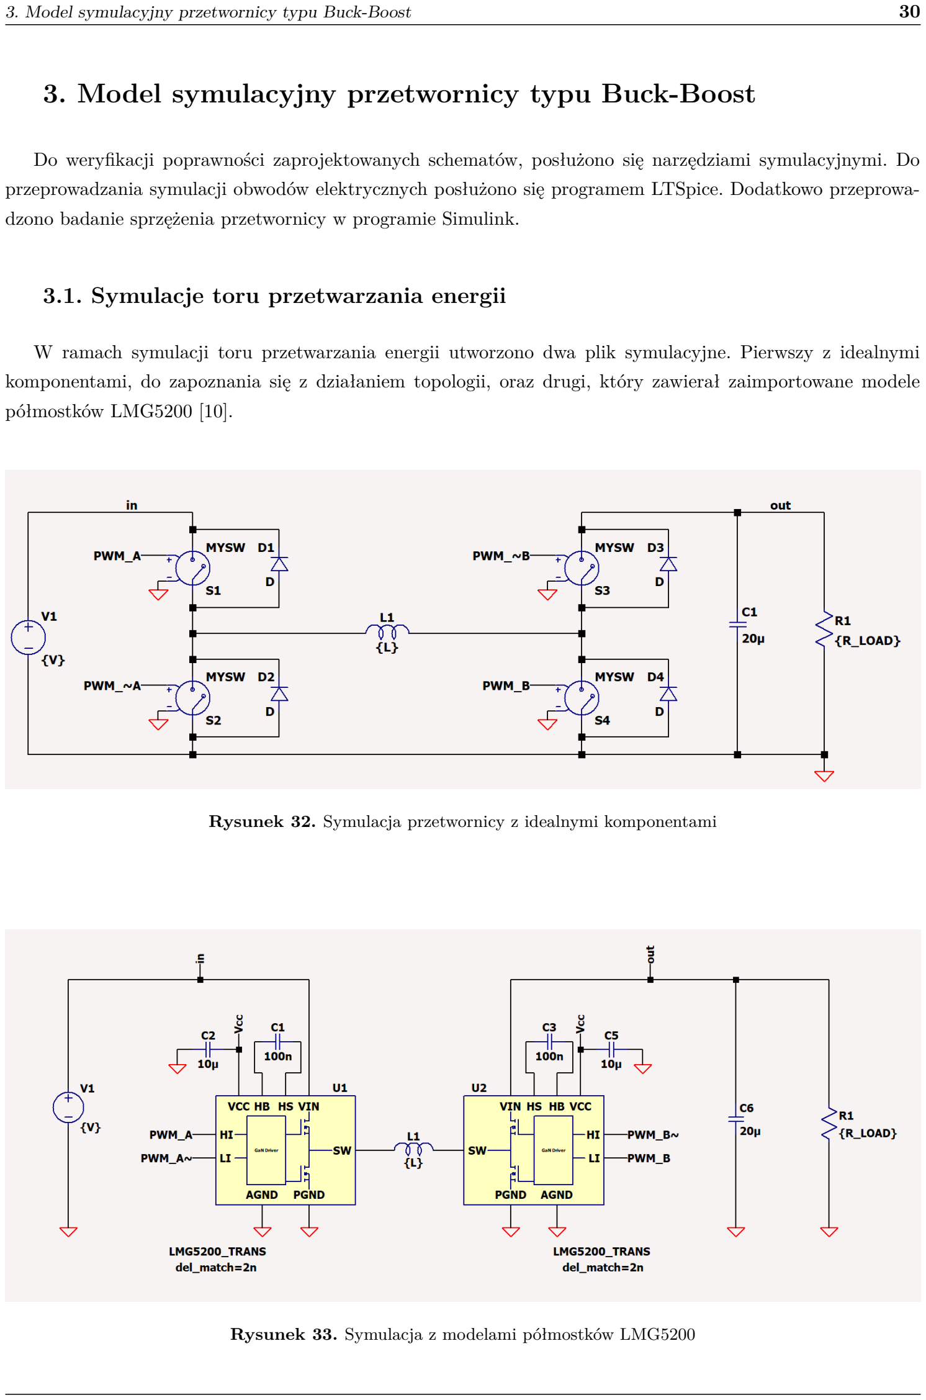
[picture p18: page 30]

3. Model symulacyjny przetwornicy typu Buck-Boost | 30

Do weryfikacji poprawności zaprojektowanych schematów, posłużono się narzędziami symulacyjnymi. Do przeprowadzania symulacji obwodów elektrycznych posłużono się programem LTSpice. Dodatkowo przeprowadzono badanie sprzężenia przetwornicy w programie Simulink.

### 3.1. Symulacje toru przetwarzania energii

W ramach symulacji toru przetwarzania energii utworzono dwa plik symulacyjne. Pierwszy z idealnymi komponentami, do zapoznania się z działaniem topologii, oraz drugi, który zawierał zaimportowane modele półmostków LMG5200 [10].

Rysunek 32. Symulacja przetwornicy z idealnymi komponentami

Rysunek 33. Symulacja z modelami półmostków LMG5200

3. Model symulacyjny przetwornicy typu Buck-Boost | 31

Tabela 4. Wyniki symulacji, założenia: VIN = 12V , RLOAD = 10Ω, fSW = 100kHz

Wypełnienie PWM -(D1, D2) | UW Y , wzór 2.1 [V] | UW Y , symulacja z idealnymi kompo-nentami [V] | UW Y , symulacja z półmostkami LMG5200 [V]
(0.25, 0) | 3 | 2.97 | 2.98
(0.5, 0) | 6 | 5.95 | 5.95
(0.75, 0) | 9 | 8.93 | 8.93
(0.75, 0.15) | 10.59 | 10.47 | 10.49
(0.75, 0.25) | 12 | 11.83 | 11.87
(0.75, 0.35) | 13.85 | 13.59 | 13.66
(1, 0.25) | 16 | 15.76 | 15.80
(1, 0.4) | 20 | 19.56 | -
(1, 0.5) | 24 | 23.27 | -

Tabela 5. Wyniki symulacji, założenia: VIN = 12V , RLOAD = 10Ω, fSW = 200kHz

Wypełnienie PWM -(D1, D2) | UW Y , wzór 2.1 [V] | UW Y , symulacja z idealnymi kompo-nentami [V] | UW Y , symulacja z półmostkami LMG5200 [V]
(0.25, 0) | 3 | 2.96 | 2.98
(0.5, 0) | 6 | 5.94 | 5.95
(0.75, 0) | 9 | 8.92 | 8.93
(0.75, 0.15) | 10.59 | 10.46 | 10.50
(0.75, 0.25) | 12 | 11.82 | 11.88
(0.75, 0.35) | 13.85 | 13.58 | -
(1, 0.25) | 16 | 15.75 | -
(1, 0.4) | 20 | 19.55 | -
(1, 0.5) | 24 | 23.27 | -

Tabela 6. Wyniki symulacji, założenia: VIN = 12V , RLOAD = 10Ω, fSW = 300kHz

Wypełnienie PWM -(D1, D2) | UW Y , wzór 2.1 [V] | UW Y , symulacja z idealnymi kompo-nentami [V] | UW Y , symulacja z półmostkami LMG5200 [V]
(0.25, 0) | 3 | 2.95 | 2.98
(0.5, 0) | 6 | 5.93 | 5.93
(0.75, 0) | 9 | 8.91 | 8.90
(0.75, 0.15) | 10.59 | 10.44 | 10.50
(0.75, 0.25) | 12 | 11.80 | 11.89
(0.75, 0.35) | 13.85 | 13.56 | 13.69
(1, 0.25) | 16 | 15.73 | -
(1, 0.4) | 20 | 19.53 | -
(1, 0.5) | 24 | 23.24 | -

3. Model symulacyjny przetwornicy typu Buck-Boost | 32

W tabelach 4, 5, 6, przedstawiono wyniki symulacji. Wartości, które zostały zmierzone, zbliżone są do wartości teoretycznych. Potwierdza to prawidłowe wykorzystanie topologii oraz poprawne użycie komponentów LMG5200 w przetwornicy. Niektóre pola w tych tabelach, znajdujące się w kolumnie dotyczącej symulacji półmostka LMG5200, są puste. Jest to spowodowanie brakiem możliwości przesymulowania układu dla tych parametrów symulacji. Model półmostka został pobrany ze strony producenta i nie jest od dedykowany do pracy w programie LTSpice. Podczas próby symulacji program zwraca informację o zbyt małym kroku czasowym symulacji i się zawiesza. Związane jest to ze zbyt dużym skomplikowaniem modelu lub jego złą optymalizacją.

Zbadano również sprawność przetwornicy w trzech trybach pracy: Buck, Buck-Boost oraz Boost. Paramatry symulacji opisano w tabeli 7. Napięcie było zmieniane krokowo, co 1V, do momentu osiągnięcia mocy wyjściowej bliskiej wartości 50W lub do momentu otrzymania błędu związanego ze zbyt małym krokiem czasowym.

Tabela 7. Parametry symulacji badającej sprawność przetwornicy

Tryb pracy | Zakres napięć wejściowych [V] | RLOAD[Ω] | fSW [kHz] | (D1, D2)
Buck | 7 ÷ 18 | 2 | 100 | (0.5, 0)
Buck-Boost | 4 ÷ 20 | 10 | 100 | (0.75, 0.25)
Boost | 4 ÷ 17 | 10 | 100 | (1, 0.25)

Rysunek 34. Sprawność przetwornicy w trzech trybach pracy

### 3.2. Symulacje modułów pomiarowych

### 3.2.1. Symulacje wzmacniaczy izolowanych AMC

Przeprowadzono symulację układów pomiaru prądu (sekcja 2.7.1), pomiaru napięcia (sekcja 2.7.3) oraz konwertera sygnału na sygnał różnicowy, wykorzystywanego w pomiarze prądu czujnikiem Halla (sekcja 2.7.2).

Modele układów AMC3302 [5] oraz AMC3330 [6] są dostępne na stronie producenta i, po drobnych zmianach,

było możliwe ich zaimportowanie do programu LTSpice. Wykonano symulacje parametryczne, korzystając z dyrektywy .param, aby określić dokładność pomiaru. Wartościami parametryzowanymi były: wartość źródła prądowego dla układu AMC3302 i wartość źródła napięcia dla układu AMC3330.

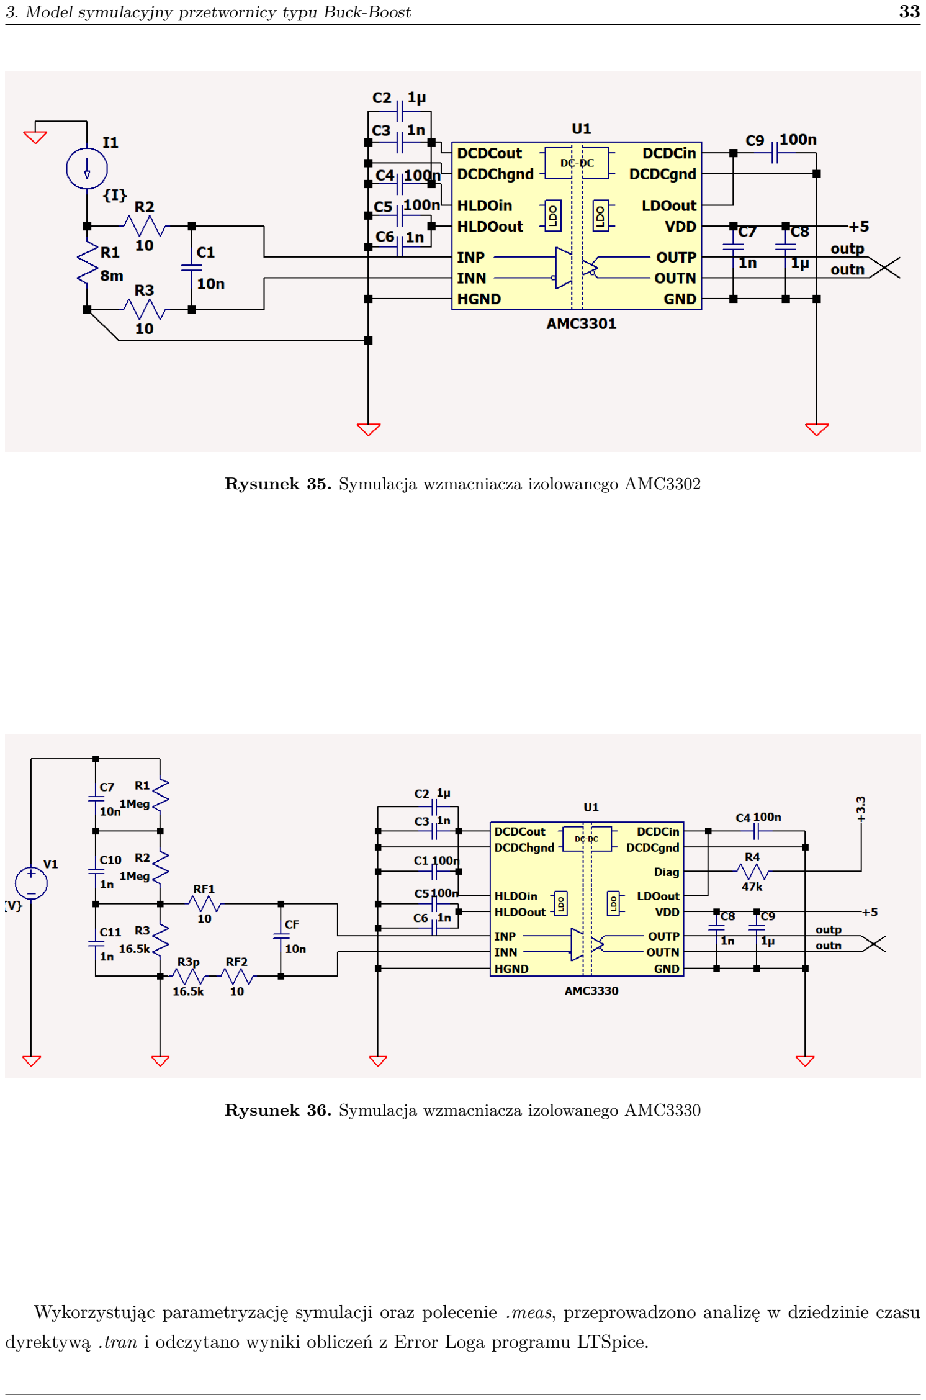
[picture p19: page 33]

3. Model symulacyjny przetwornicy typu Buck-Boost | 33

Rysunek 35. Symulacja wzmacniacza izolowanego AMC3302

Rysunek 36. Symulacja wzmacniacza izolowanego AMC3330

Wykorzystując parametryzację symulacji oraz polecenie .meas, przeprowadzono analizę w dziedzinie czasu dyrektywą .tran i odczytano wyniki obliczeń z Error Loga programu LTSpice.

3. Model symulacyjny przetwornicy typu Buck-Boost | 34

Tabela 8. Wyniki symulacji układu AMC3302

Wartość na źró-dle prądu [A] | Napięcie na wyj-ściu wzmacnia-cza [A] | Zmierzony prąd [A] | Dokładność [A]
0.1 | 0.0063 | 0.096 | 0.0037
0.2 | 0.13 | 0.196 | 0.0039
0.5 | 0.032 | 0.496 | 0.0045
0.75 | 0.49 | 0.745 | 0.0055
1 | 0.065 | 0.995 | 0.0055
2 | 0.13 | 1.98 | 0.017
5 | 0.3171 | 4.987 | 0.013

Tabela 9. Wyniki symulacji układu AMC3330

Wartość na źró-dle napięcia [V] | Napięcie na wyj-ściu wzmacnia-cza [V] | Zmierzone na-pięcie [V] | Dokładność [V]
5 | 0.082 | 5.0073 | 0.0073
10 | 0.16 | 10.0022 | 0.0022
12 | 0.20 | 12.00013 | 0.00013
15 | 0.25 | 14.99695 | 0.0030
20 | 0.33 | 19.9917 | 0.0083

Symulacje pokazują, że wzmacniacze AMC cechują się dużą dokładnością przy pomiarach DC. Ich dokładność jest na poziomie poniżej jednego punktu procentowego a maksymalne odchylenie od wartości wejściowej jest na poziomie pojedynczych miliwoltów/miliamperów.

### 3.2.2. Symulacje wzmacniacza LTC6362

Przy konwersji z sygnału mierzonego względem masy na sygnał różnicowy posłużono się układem LTC6362 [12].

3. Model symulacyjny przetwornicy typu Buck-Boost | 35

Rysunek 37. Symulacja różnicowego sterownika ADC LTC6362

Zbadano stabilność układu oraz zweryfikowano poprawność konwersji sygnału wykorzystując analizę przebiegów czasowych .tran. Jako sygnał wejściowy wybrano falę trójkątna o amplitudzie 1V, oscylującą wokół wartości 2.5V i częstotliwości 100kHz. Taki przebieg ma reprezentować przykładowy sygnał, który może zostać wyprodukowany przez sensor prądu ACS730 [3].

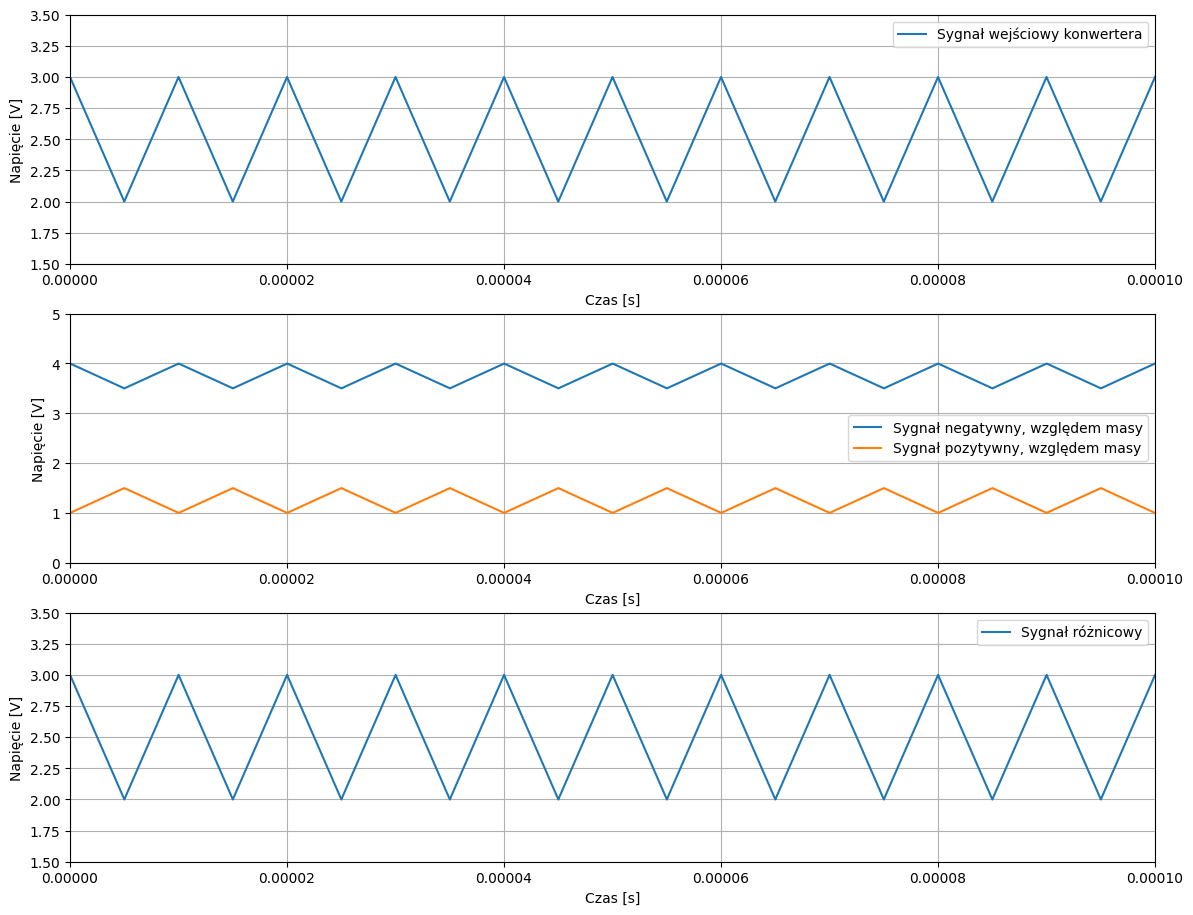
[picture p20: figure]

Rysunek 38. Weryfikacja poprawności konwersji sygnału na różnicowy

### 3.3. Symulacje filtrów

Do zweryfikowania poprawności działania filtrów pasywnych wykorzystano dyrektywę .ac. Dzięki temu zbadano filtr EMI, filtr wejściowy oraz filtr wyjściowy w domenie częstotliwości, weryfikując poprawność obliczeń opisanych w sekcjach 2.8.1, 2.8.2, 2.8.3. Przy symulacjach zadbano o uzupełnienie modeli komponentów C i L

3. Model symulacyjny przetwornicy typu Buck-Boost | 36

o ich wartości pasożytnicze tak aby uzyskana charakterystyka częstotliwościowa była jak najbardziej zbliżona do charakterystyki rzeczywistej filtru.
Wartości tłumienia uzyskane z tych symulacji, w szczególności dla częstotliwości rzędu kilku MHz-ów, są bardzo niskie. Na tyle niskie, że fizyczne wykonanie takiego filtru byłoby niemożliwe. Zbyt duże wartości tłumienia, poniżej -150dB, są związane z nieodpowiednim zamodelowaniem filtrów. Pomimo dodania wartości pasożytniczych, symulowane układy nadal potrafią osiągnąć tłumienie rzędu -160dB co sugeruje niedokładne wykonanie modelu.

### 3.3.1. Symulacje filtru EMI

Przy symulacji filtru EMI, omówionego w sekcji 1.5, dodano model dławika common-mode [2], dostępny na

stronie producenta. Dzięki dodawaniu rzeczywistych modeli do symulacji uzyskiwane charakterystyki zyskują na dokładności.

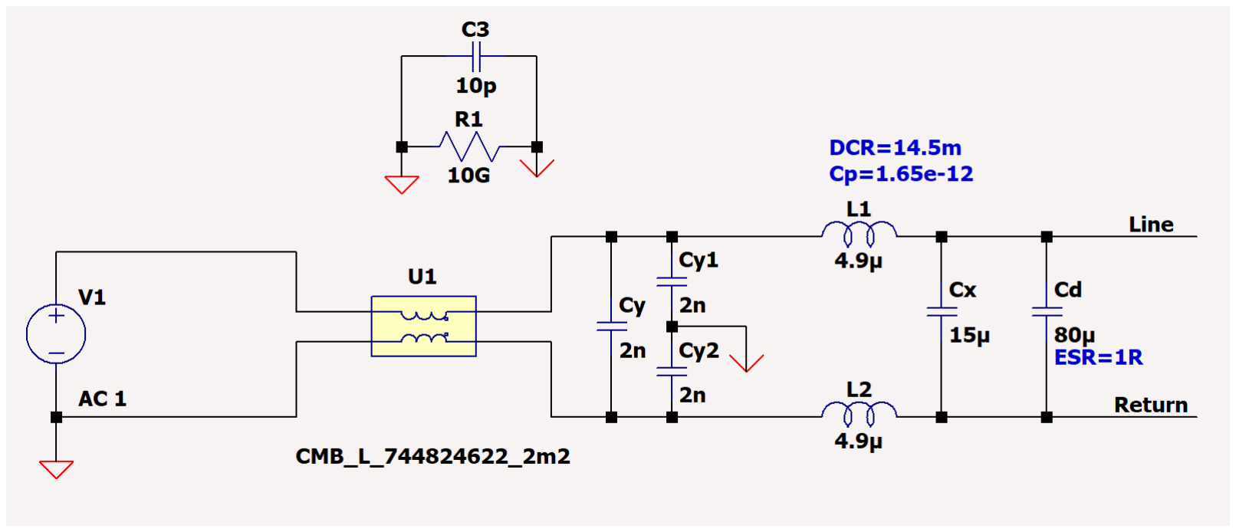
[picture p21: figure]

Rysunek 39. Symulacja filtru EMI

Rysunek 40. Charakterystyka częstotliwościowa filtru EMI

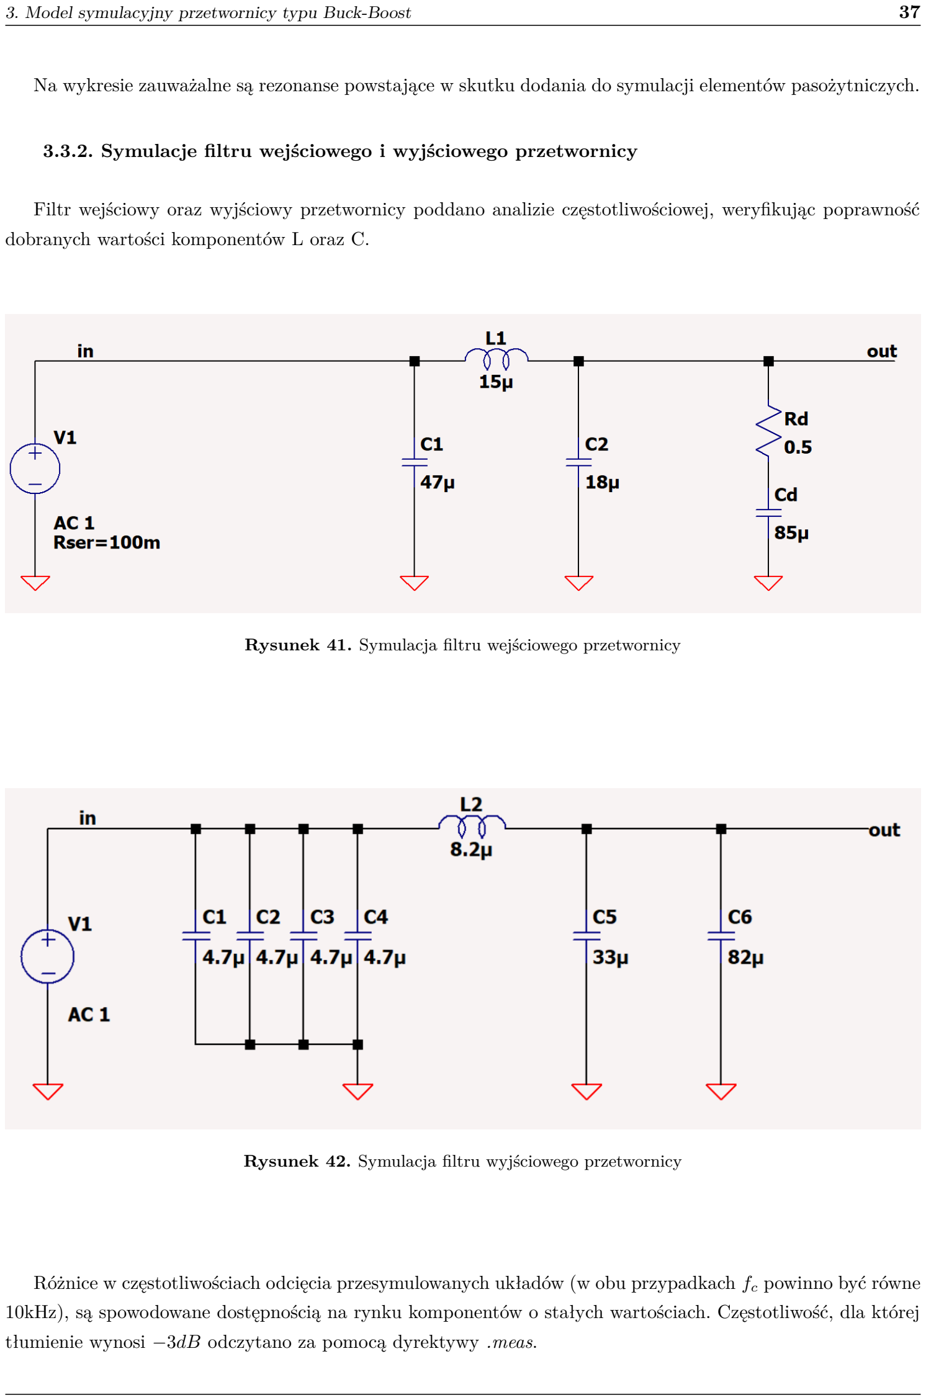
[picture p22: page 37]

3. Model symulacyjny przetwornicy typu Buck-Boost | 37

Na wykresie zauważalne są rezonanse powstające w skutku dodania do symulacji elementów pasożytniczych.

### 3.3.2. Symulacje filtru wejściowego i wyjściowego przetwornicy

Filtr wejściowy oraz wyjściowy przetwornicy poddano analizie częstotliwościowej, weryfikując poprawność dobranych wartości komponentów L oraz C.

Rysunek 41. Symulacja filtru wejściowego przetwornicy

Rysunek 42. Symulacja filtru wyjściowego przetwornicy

Różnice w częstotliwościach odcięcia przesymulowanych układów (w obu przypadkach fc powinno być równe 10kHz), są spowodowane dostępnością na rynku komponentów o stałych wartościach. Częstotliwość, dla której tłumienie wynosi −3dB odczytano za pomocą dyrektywy .meas.

3. Model symulacyjny przetwornicy typu Buck-Boost | 38

Rysunek 43. Charakterystyka częstotliwościowa filtru wejściowego przetwornicy

Rysunek 44. Charakterystyka częstotliwościowa filtru wyjściowego przetwornicy

Tabela 10. Porównanie częstotliwości odcięcia filtrów: wejściowego i wyjściowego

| fc zamierzone [kHz] | fc z wartościami idealnych kompo-nentów [kHz] | punkt −3dB od-czytany z symulacji [kHz]
Filtr wejściowy | 10 | 9.69 | 11.97
Filtr wyjściowy | 10 | 9.68 | 11.63

3. Model symulacyjny przetwornicy typu Buck-Boost | 39

### 3.4. Symulacje pętli sprzężenia zwrotnego przetwornicy

W celu zapoznania się z teorią sterowania przetwornic DC-DC, utworzono prostą symulacją przetwornicy Buck-Boost, opartej na 4 kluczach tranzystorowych, pracującej w trybie Buck.

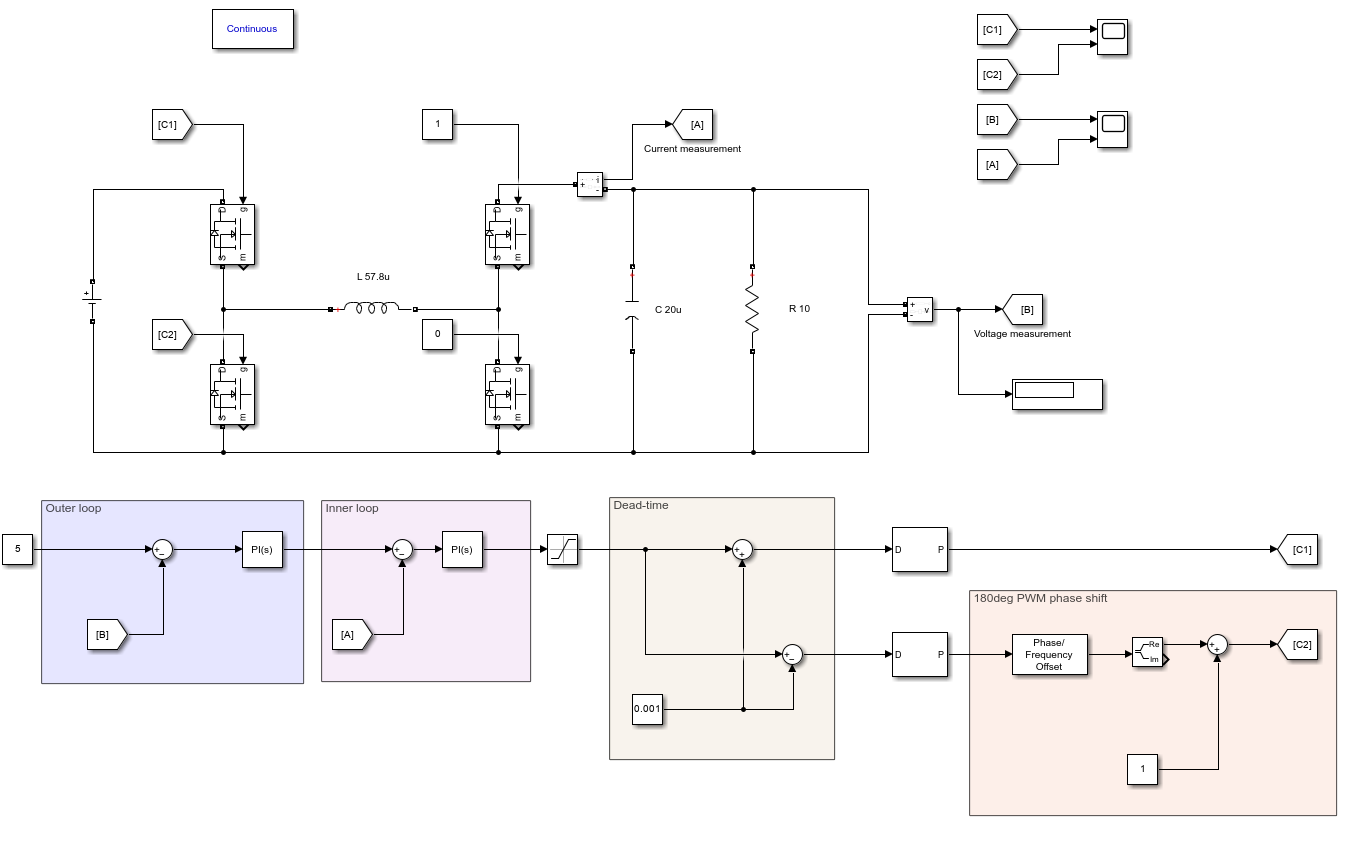
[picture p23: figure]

Rysunek 45. Pętla sterowania zrealizowana w programie Simulink

Pozwoliło to na zaobserwowanie problemów dotyczących sterowania, a dokładniej kalibracji kontrolerów PI, opisanych w sekcji 1.4. Utworzony model nie odpowiada dokładnie realizowanemu systemowi. Dlatego nie zdecydowano się na przeniesienie, uzyskanych w trakcie kalibracji kontrolerów PI, wartości wzmocnień KP oraz KI . Algorytm, odpowiedzialny za sterowanie, zostanie opisany w sekcji 4.1.

4. Cyfrowa pętla sprzężenia zwrotnego | 40

## 4. Cyfrowa pętla sprzężenia zwrotnego

Do utrzymania stałego napięcia wyjściowego przetwornicy DC-DC wykorzystywane jest sprzężenie zwrotne. W poniższym rozdziale zostanie opisany algorytm wykorzystany do sterowania przetwornicą Buck-Boost oraz jego implementacja na mikrokontrolerze STM32G474 [13].

### 4.1. Opis zastosowanego algorytmu

Ilość pomiarów wykonywanych na płytce PCB, sekcja 2.7, pozwala na implementację bardzo dużej ilości algorytmów sterowania. Jako docelowy algorytm kontrolujący pętle sterowania wybrano algorytm sterowania prądem wyjściowym (ang. current-mode). [18].

Rysunek 46. Schemat blokowy algorytmu current-mode

Wartość UREF to oczekiwana wartość napięcia na wyjściu przetwornicy, jest ona porównywana do napięcia zmierzonego na wyjściu UW Y . Obliczana różnica, sygnał błędu ε

∗
, jest podawany do pierwszego regulatora PI. Ta część algorytmu jest nazywana pętlą zewnętrzną układu sterującego. Otrzymana skompensowana wartość

I

∗
jest kolejny raz porównywana, tym razem z odczytem pomiaru prądu wyjściowego IW Y . Nowy sygnał błędu ε jest podawany na wejście drugiego regulatora PI co zamyka wewnętrzną pętle. Z wartości znajdującej się na wyjściu kompensatora U

∗ otrzymywany jest współczynnik wypełnienia. Generator PWM, z takim parametrem

wejściowym, jest w stanie wytworzyć przebieg fali prostokątnej z otrzymanym współczynnikiem wypełnienia.

### 4.2. Implementacja algorytmu na mikrokontrolerze

Wykorzystanie w projekcie mikrokontrolera, daje pewnego rodzaju elastyczność i pozwoli wdrożyć różne algorytmy sterowania bez żadnych zmian w części elektronicznej projektu. Jest to znacząca przewaga nad klasycznymi kontrolerami, które projektowane są pod konkretną topologię przetwornicy, i nie zapewniają możliwości zmian algorytmu sterowania bez zmian w projekcie płytki PCB.
Aby wdrożyć zaproponowany algorytm wymagana jest konfiguracja układów peryferyjnych mikrokontrolera STM32G474. Do najważniejszych peryferiów wymagających konfiguracji należą: HRTIM - High Resolution Timer, liczniki o dużej rozdzielczości, ADC - Analog to Digital Converter, przetworniki analogowo cyfrowe oraz DMA - Direct Memory Access.

### 4.2.1. Konfiguracja peryferiów mikrokontrolera - liczniki HRTIM

Konfiguracja liczników została przeprowadzona w IDE dostarczonym przez producenta mikrokontrolera, STM Cube IDE. W tym środowisku konfiguracja odbywa się poprzez zaznaczanie funkcjonalności peryferiów, które są dla nas interesujące, a następnie, dzięki wygenerowanemu API, możliwe jest skorzystanie z gotowych funkcji dostarczonych dzięki sterownikowi HAL.

4. Cyfrowa pętla sprzężenia zwrotnego | 41

W zakładce Timers/HRTIM wybrano dwa liczniki, które zostały użyte - Timer A oraz Timer B. Oba

liczniki będę generowane komplementarnie, co skutkuje finalnie w otrzymaniu czterech sygnałów do sterowania odpowiednimi półmostkami, sygnałami TA1, TA2, TB1 oraz TB2.

W zakładce Configuration znajduje się kilka pól wymagających wprowadzenia danych przez użytkownika. Pole Timer A/B zawiera ogólne informacje na temat sygnałów PWM. Tam definiowane są parametry czasowe przebiegów, ustawianie czasu martwego oraz jednostek porównawczych (potrzebnych do modulacji wypełnieniem przebiegu). Oprócz tego w polu ADC Trigger Configuration, wyznaczono jednostę porównawczą 4, jako

wyzwalacz próbkowania. Zapewni to próbkowanie sygnałów w odpowiednich momentach, minimalizując szansę na to, że zakłócenia związane z przełączaniem tranzystorów będą wpływać na pomiary.

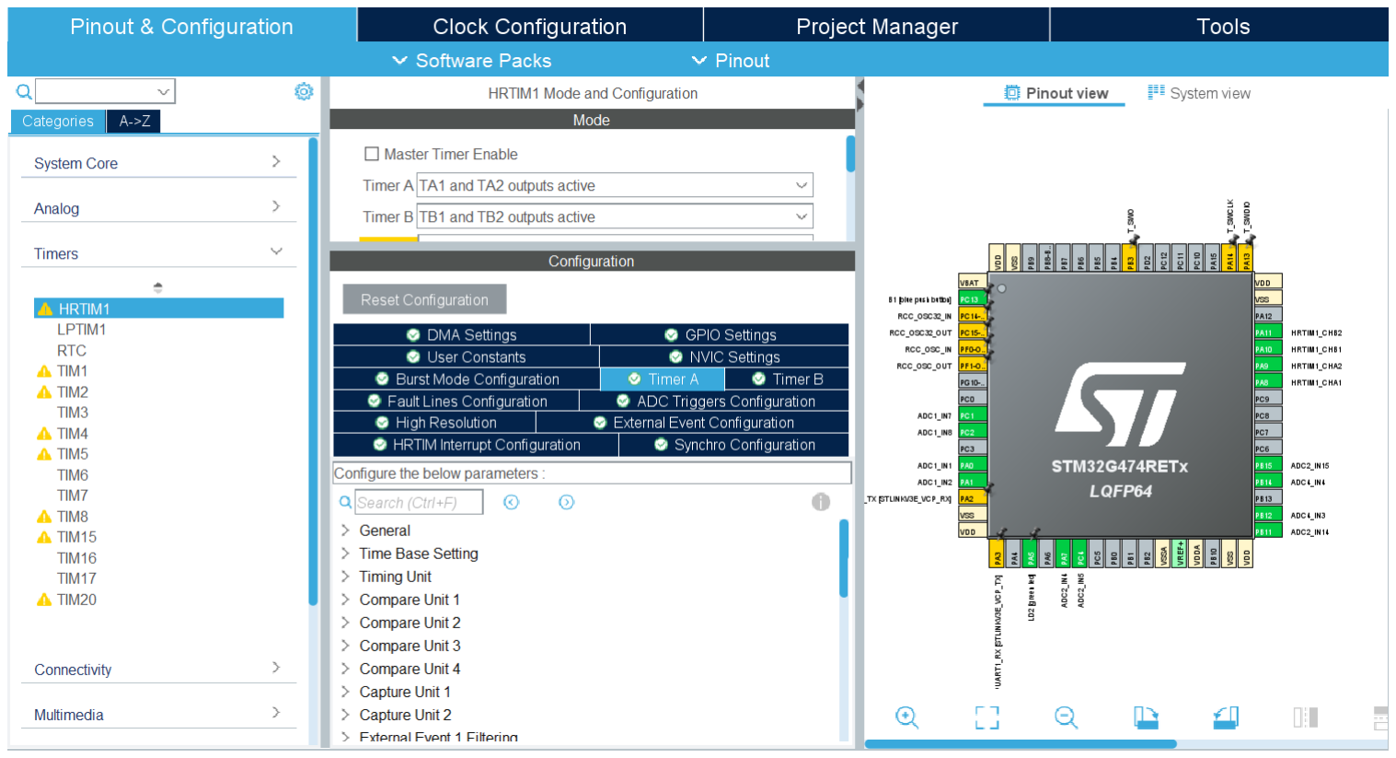
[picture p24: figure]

Rysunek 47. Widok interface’u do konfiguracji liczników HRTIM

### 4.2.2. Konfiguracja peryferiów mikrokontrolera - przetworniki analogowo cyfrowe

Przetworniki analogowo cyfrowe ADC1, ADC2 oraz ADC4, podobnie jak liczniki HRTIM, zostały skonfigurowane w CubeIDE. Łącznie wymagane jest próbkowanie pięciu sygnałów. Każdy z nich jest przesyłany do przetwornika różnicowo. W zakładce Mode możliwe jest włączenie wejść przetwornika, oraz ustawienie typu wejścia: Single-ended bądź Differential. Przetwornik ADC1 ma włączone dwa wejścia IN1 (dodatkowo I2) oraz IN6 (dodatkowo IN7). ADC2 ma również włączone dwa wejścia IN4 (IN5) i IN14 (IN15). ADC4 ma włączone jedno wejście IN3 (IN4).

W zakładce Configuration, w polu Parameter settings możliwa jest konfiguracja ogólnych ustawień przetwornika. Ważne jest ustawienie rozdzielczości przetwarzanych pomiarów, 12 bitów, oraz zewnętrznego wyzwalania konwersji, poprzez licznik HRTIM Timer A. Poniważ przetworniki ADC1 oraz ADC2, w odróżnieniu od ADC4, korzystają z więcej niż jednego wejścia, wymagane jest włączenie ustawienia Scan Conversion Mode. To ustawienie powoduje przełączania się pomiędzy dostępnymi wejściami, tak aby uzyskiwać wartości z dwóch pomiarów.

4. Cyfrowa pętla sprzężenia zwrotnego | 42

W tym miejscu można od razu skonfigurować dostęp do DMA. W zakładce DMA Settings należy dodać DMA Request. Dodanie tej prośby wygeneruje dodatkową funkcję w bibliotece HAL umożliwiającą odczytywanie wartości po konwersji bezpośrednio z pamięci.

Rysunek 48. Widok interface’u do konfiguracji przetworników ADC

### 4.2.3. Implementacja

Dzięki poprawnemu skonfigurowaniu układów peryferyjnych mikrokontrolera, możliwe jest zaimplementowania algorytmu sterowania. Wymagane funkcjonalności są widoczne na rysunku 46. Odczyty danych są realizowane przez przetworniki ADC, kontrolery PI zostały wykonane bezpośrednio na mikrokontrolerze a generator PWM został zrealizowany przy pomocy liczników HRTIM.
Do przedstawienia działania pliku main.c w projekcie wykonano diagram sekwencji działań.

4. Cyfrowa pętla sprzężenia zwrotnego | 43

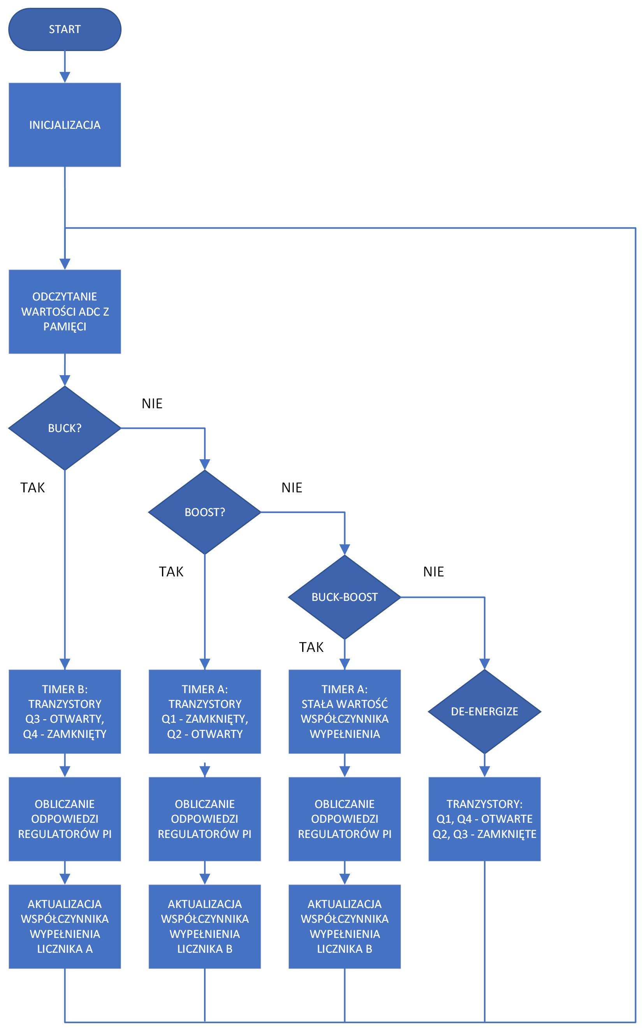
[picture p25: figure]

Rysunek 49. Diagram sekwencji działań pliku main.c

## Podsumowanie i wnioski

Proces realizacji projektu można opisać jako listę poniższych kroków:

1. Zdefiniowanie założeń projektowych.
2. Wykonanie podstawowych obliczeń dla topologii opartej na czterech kluczach tranzystorowych.
3. Narysowanie diagramu blokowego i określenie konkretnych bloków funkcyjnych w projekcie.
4. Zapoznanie się z dostępnymi na rynku rozwiązaniami i technologiami umożliwiającymi poprawę jakości przetwornicy i/lub ułatwiających projektowanie.
5. Przeprowadzenie symulacji weryfikujących poprawne działanie przetwornicy oraz układów pomiarowych.
6. Wykonanie schematu elektrycznego w programie Altium Designer.
7. Zaprojektowanie płytki drukowanej w programie Altium Designer.
8. Symulacje sprzężenia zwrotnego przetwornicy DC-DC w programie Matlab Simulink
9. Implementacja algorytmu sterowania na mikrokontrolerze STM32G474

Zaprojektowana w ten sposób przetwornica będzie mogła służyć za model laboratoryjny, z którego studenci będą mogli korzystać na zajęciach. Dalsze etapy pracy nad projektem nie zostały zrealizowane ze względu na ograniczenie czasowe. Przetwornica powinna być zmontowana i przetestowana, aby upewnić się, że model symulacyjny jest prawidłowy. Projektowanie elektroniki to proces iteracyjny, dlatego bez żadnych wątpliwości jestem w stanie stwierdzić, że w trakcie projektowania mogły się w pewnym momencie wkraść błędy. Dlatego testy projektów elektronicznych są niezmiernie ważne i pozwalają w przyszłości unikać popełnionych błędów. Poza przeprowadzeniem testów w otwartej pętli, weryfikując poprawność zaprojektowania przetwornicy, wymagane będzie przeprowadzenie testów w zamkniętej pętli sterowania. Wyniki symulacji sprzężenie zwrotnego, wykonane w Simulinku, nie dały miarodajnych wyników pozwalających na kalibrację kontrolerów PI. Dobór wzmocnień KP oraz KI będzie stanowić ważne zadanie przy tych testach. Możliwe będzie zaimplementowanie innych algorytmów kontroli. Wykorzystanie prądu dławika w algorytmie lub zmiana modulacji sygnału sterującego bramki tranzystora to tylko kilka możliwości, które umożliwiają zmianę działania pętli sterowania przetwornicy.

Zaprojektowanie przetwornicy Buck-Boost pomogło przybliżyć tematykę impulsowych przetwornicy DC-DC. Dzięki zrozumieniu działania podstawowych topologii przetwornic, możliwe było zaprojektowanie układu opierającego się na czterech kluczach tranzystorowych. W trakcie projektowania zagłębiono się w tematykę sterowania. Zaczynając od prostych kontrolerów, kończąc na algorytmach. Teoria sterowania wymusiła umieszczenie w przetwornicy kilku bloków funkcyjnych, które umożliwiały realizację cyfrowego sprzężenia zwrotnego. Ich symulacje pokazały jak potrzebnym narzędziem, w projektowaniu układów elektronicznych, są programy umożliwiające weryfikację działania każdego zamodelowanego układu scalonego. Projektowanie filtrów uzmysłowiło, jak ważne jest zadbanie o poprawność modeli komponentów i zawarcie wszsytkich parametrów, a przede wszystkim pasożytniczych, w symulacjach.

SPIS RYSUNKÓW | 45

# Spis rysunków

1 | Przetwornica typu Buck | | 5
2 | Przetwornica typu Boost | | 6
3 | Odwracająca przetwornica typu Buck-Boost | | 7
4 | Przetwornica typu Buck-Boost na czterech kluczach | | 8
5 | Przykład realizacji sprzężenia zwrotnego na przetwornicy Buck | | 9
6 | Schemat blokowy kontrolera PID | | 9
7 | Typy odpowiedzi regulatora PID, [9] | 10
8 | Zobrazowanie zakłóceń różnicowych | 11
9 | Zobrazowanie zakłóceń wspólnych | 11
10 | Filtr EMI | 12
11 | Przetwornica Buck-Boost w trybie Buck | 14
12 | Przetwornica Buck-Boost w trybie Boost | 15
13 | Przetwornica Buck-Boost w trybie mieszanym | 15
14 | Schemat blokowy przetwornicy Buck-Boost | 17
15 | Fragment schematu zawierający izolowany zasilacz NXJ1S0505MC | 19
16 | Fragment schematu zawierający cyfrowy izolator ADuM340E | 19
17 | Schemat ideowy układu crowbar | 20
18 | Fragment schematu zawierający układ protekcyjny | 20
19 | Schemat ideowy układu pomiaru prądu z rezystorem typu shunt | 21
20 | Fragment schematu zawierający układu pomiaru prądu z rezystorem typu shunt | 22
21 | Fragment schematu zawierający sensor prądu ACS730 | 22
22 | Schemat ideowy pomiaru napięcia na dzielniku | 23
23 | Fragment schematu zawierający układ pomiaru napięcia | 23
24 | Fragment schematu zawierający układ punktu pomiarowego | 24
25 | Fragment schematu zawierający układ filtru EMI | 25
26 | Filtr typu Pi | 25
27 | Filtr EMI typi Pi z dołączonymi elementami Cd i Rd | 26
28 | Fragment schematu zawierający układ filtru wejściowego | 27
29 | Fragment schematu zawierający układ filtru wyjściowego | 27
30 | Widok płytki PCB z zaznaczonymi blokami funkcyjnymi | 28
31 | Stackup płytki czterowarstwowej, [16] | 29

32 | Symulacja przetwornicy z idealnymi komponentami | 30
33 | Symulacja z modelami półmostków LMG5200 | 30
34 | Sprawność przetwornicy w trzech trybach pracy | 32
35 | Symulacja wzmacniacza izolowanego AMC3302 | 33
36 | Symulacja wzmacniacza izolowanego AMC3330 | 33
37 | Symulacja różnicowego sterownika ADC LTC6362 | 35
38 | Weryfikacja poprawności konwersji sygnału na różnicowy | 35
39 | Symulacja filtru EMI | 36
40 | Charakterystyka częstotliwościowa filtru EMI | 36
41 | Symulacja filtru wejściowego przetwornicy | 37
42 | Symulacja filtru wyjściowego przetwornicy | 37
43 | Charakterystyka częstotliwościowa filtru wejściowego przetwornicy | 38
44 | Charakterystyka częstotliwościowa filtru wyjściowego przetwornicy | 38
45 | Pętla sterowania zrealizowana w programie Simulink | 39
46 | Schemat blokowy algorytmu current-mode | 40
47 | Widok interface’u do konfiguracji liczników HRTIM | 41
48 | Widok interface’u do konfiguracji przetworników ADC | 42
49 | Diagram sekwencji działań pliku main.c | 43

# Spis tabel

1 | Założenie projektowe przetwornicy Buck-Boost | 14
2 | Minimalne wartości indukcyjności dławika | 18
3 | Wybrane induktory | 18
4 | Wyniki symulacji, założenia: VIN = 12V , RLOAD = 10Ω, fSW = 100kHz | 31
5 | Wyniki symulacji, założenia: VIN = 12V , RLOAD = 10Ω, fSW = 200kHz | 31
6 | Wyniki symulacji, założenia: VIN = 12V , RLOAD = 10Ω, fSW = 300kHz | 31
7 | Parametry symulacji badającej sprawność przetwornicy | 32
8 | Wyniki symulacji układu AMC3302 | 34
9 | Wyniki symulacji układu AMC3330 | 34
10 | Porównanie częstotliwości odcięcia filtrów: wejściowego i wyjściowego | 38

SPIS RÓWNAŃ | 47

# Spis równań

1.1 | Współczynnik wypełnienia sygnału PWM | | 5
1.2 | Napięcie wyjściowe przetwornicy Buck | | 6
1.5 | Napięcie wyjściowe przetwornicy Boost | | 7
1.6 | Napięcie wyjściowe odwracającej przetwornicy Buck-Boost | | 7
1.7 | Sprawność układu | | 8
1.8 | Dobroć układu RLC | 12
1.9 | Rezystancja Rd | 12
2.1 | Napięcie wyjściowe przetwornicy Buck-Boost, 4 klucze | 15
2.2 | Minimalna wartość induktancji dla przetwornicy typu Buck | 17
2.3 | Minimalna wartość induktancji dla przetwornicy typu Boost | 17
2.4 | Odczytanie wartości prądu płynącego przez rezystor shunt | 21
2.5 | Wzór dzielnik napięcia | 23
2.6 | Odczytanie wartości napięcia w węźle | 23
2.7 | Częstotliwość odcięcia filtru dolnoprzepustowego LC | 24
2.8 | Dobroć układu filtrującego | 26

## Bibliografia

[1] Dragan Maksimović Robert W. Erickson. Fundamentals of Power Electornics, Third Edition. Springer,

2020.

[2] 744824622. Common-mode choke. url: https:// www.we-online.com/ components/ products/ datasheet/

744824622.pdf (https://www.we-online.com/components/products/datasheet/744824622.pdf) .

[3] ACS730. Isolated current sensor. url: https : // www .allegromicro .com/ en/ Products/ Sense/ Current -Sensor-ICs/ Zero-To-Fifty-Amp-Integrated-Conductor-Sensor-ICs/ ACS730 (https://www.allegromicro.com/en/Products/Sense/Current-Sensor-ICs/Zero-To-Fifty-Amp-Integrated-Conductor-Sensor-ICs/ACS730) .
[4] ADUM340E. Digital isolator. url: https:// www.analog.com/ media/ en/ technical-documentation/ data-sheets/ adum340e-341e-342e.pdf (https://www.analog.com/media/en/technical-documentation/data-sheets/adum340e-341e-342e.pdf) .
[5] AMC3302. Isolated current sensig amplifier. url: https://www.ti.com/ lit/ ds/ symlink/ amc3302.pdf (https://www.ti.com/lit/ds/symlink/amc3302.pdf) .
[6] AMC3330. Isolated voltage sensing amplifier. url: https://www.ti.com/ lit/ ds/ symlink/ amc3330.pdf (https://www.ti.com/lit/ds/symlink/amc3330.pdf) .
[7] Julian Hagedorn. Basic Calculations of a 4 Switch Buck-Boost Power Stage. url: https:// www.ti.com/ lit/ an/ slva535b/ slva535b.pdf (https://www.ti.com/lit/an/slva535b/slva535b.pdf) .
[8] Shawn Hymel. Introduction to PID Controllers. url: https : // www .digikey .com/ en/ maker/ projects/ introduction-to-pid-controllers/ 763a6dca352b4f2ba00adde46445ddeb. (https://www.digikey.com/en/maker/projects/introduction-to-pid-controllers/763a6dca352b4f2ba00adde46445ddeb)
[9] Introducción a PID. url: https : / / docs . wpilib . org / es / latest / docs / software / advanced - controls / introduction/ introduction-to-pid.html. (https://docs.wpilib.org/es/latest/docs/software/advanced-controls/introduction/introduction-to-pid.html)
[10] LMG5200MOFT. GaN Half-Bridge Power Stage. url: https://www.ti.com/ lit/ ds/ symlink/ lmg5200.pdf (https://www.ti.com/lit/ds/symlink/lmg5200.pdf) .
[11] LTC6262. 30MHz bandwidth amplifier. url: https : / / www . analog . com / media / en / technical -documentation/ data-sheets/ 626123fa.pdf (https://www.analog.com/media/en/technical-documentation/data-sheets/626123fa.pdf) .
[12] LTC6362. Precision amplifier. url: https:// www.analog.com/ media/ en/ technical-documentation/ data-sheets/ 6362fa.pdf (https://www.analog.com/media/en/technical-documentation/data-sheets/6362fa.pdf) .
[13] Nucleo G474RE. MCU evaluation board. url: https : / / www . st . com / en / evaluation - tools / nucleo -

g474re.html. (https://www.st.com/en/evaluation-tools/nucleo-g474re.html)

[14] NXJ1S0505MC. Isolated power supply. url: https : / / www . murata . com / products / productdata / 8807031963678/ kdc-nxj1.pdf (https://www.murata.com/products/productdata/8807031963678/kdc-nxj1.pdf) .
[15] PA2050. Power inductor. url: https:// productfinder.pulseelectronics.com/ api/ open/ part-attachments/ datasheet/ pa2050.103nl. (https://productfinder.pulseelectronics.com/api/open/part-attachments/datasheet/pa2050.103nl)
[16] Zachariah Peterson. How to Design and Fabricate the Best 4 Layer PCB Stackup with Altium Designer. url: https:// docs.wpilib.org/ es/ latest/ docs/ software/ advanced-controls/ introduction/ introduction-to-

pid.html. (https://docs.wpilib.org/es/latest/docs/software/advanced-controls/introduction/introduction-to-pid.html)

BIBLIOGRAFIA | 49
[17] ROHM semiconductors. Design and Application Considerations of Input Filter to reduce Conducted Emissions caused by DC/DC converter. url: https:// fscdn.rohm.com/ en/ products/ databook/ applinote/ ic/ power/ input-filter-for-dcdc-converter_an-e.pdf (https://fscdn.rohm.com/en/products/databook/applinote/ic/power/input-filter-for-dcdc-converter_an-e.pdf) .
[18] Robert Sheehan. Understanding and Applying Current-Mode Control Theory. url: https:// www.ti.com/ lit/ an/ snva555/ snva555.pdf (https://www.ti.com/lit/an/snva555/snva555.pdf) .
[19] Paul Shepard. Understanding Isolation in DC-DC Converters. url: https : / / eepower . com / news / understanding-isolation-in-dc-dc-converters/#. (https://eepower.com/news/understanding-isolation-in-dc-dc-converters/#)
[20] Ali Shirsavar. EMC Filter Design. url: https://www.biricha.com/ technical-videos.html. (https://www.biricha.com/technical-videos.html)
[21] TPS1HB16-Q1. High-side switch. url: https://www.ti.com/ lit/ ds/ symlink/ tps1hb16-q1.pdf (https://www.ti.com/lit/ds/symlink/tps1hb16-q1.pdf) .

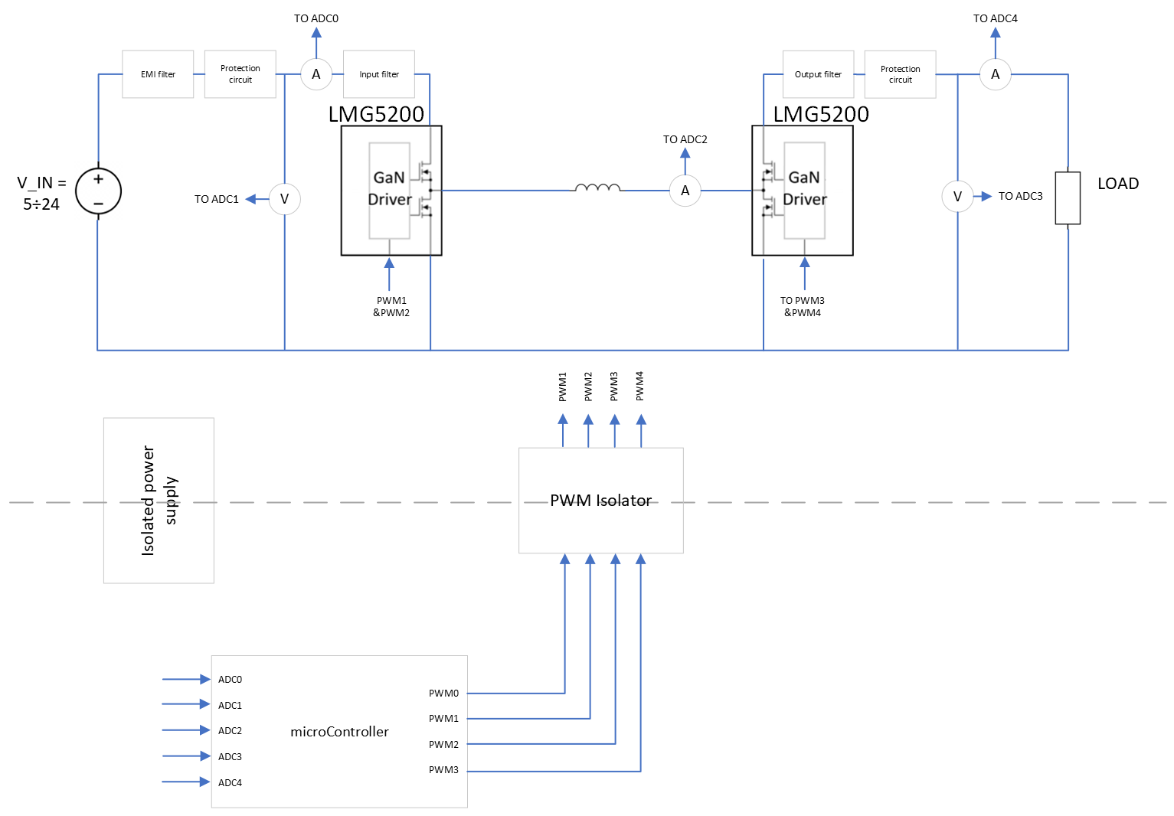
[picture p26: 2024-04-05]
images/drawing/DCDC_BuckBoost_BlockSchematic.png

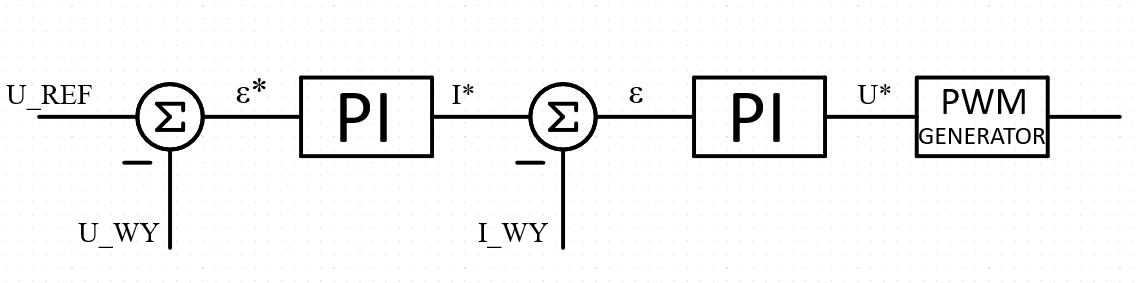
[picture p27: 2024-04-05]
images/drawing/control_system.png

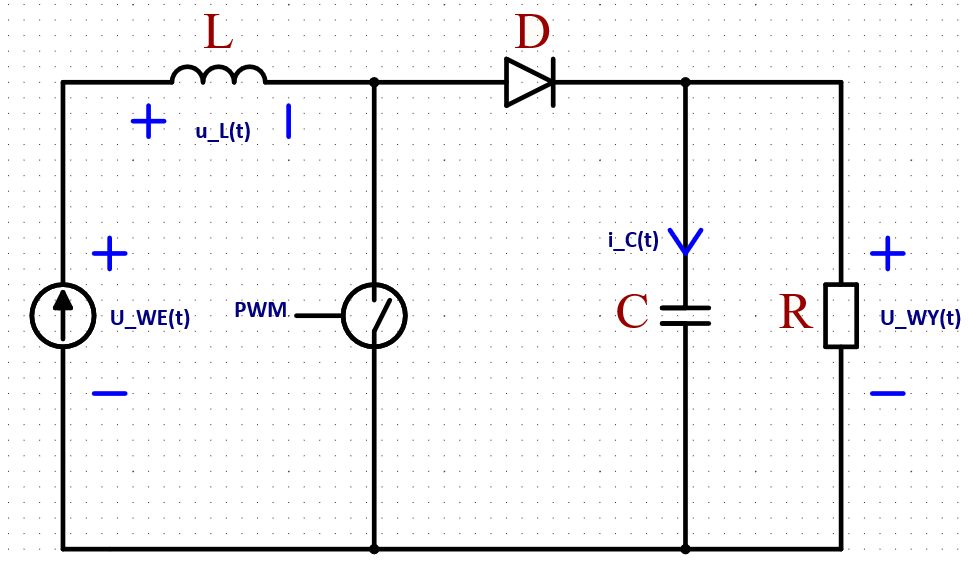
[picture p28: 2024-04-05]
images/drawing/Boost_topology.png

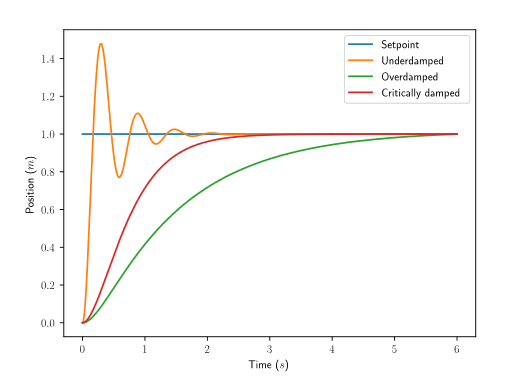
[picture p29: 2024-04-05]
images/plots/PID_response.png

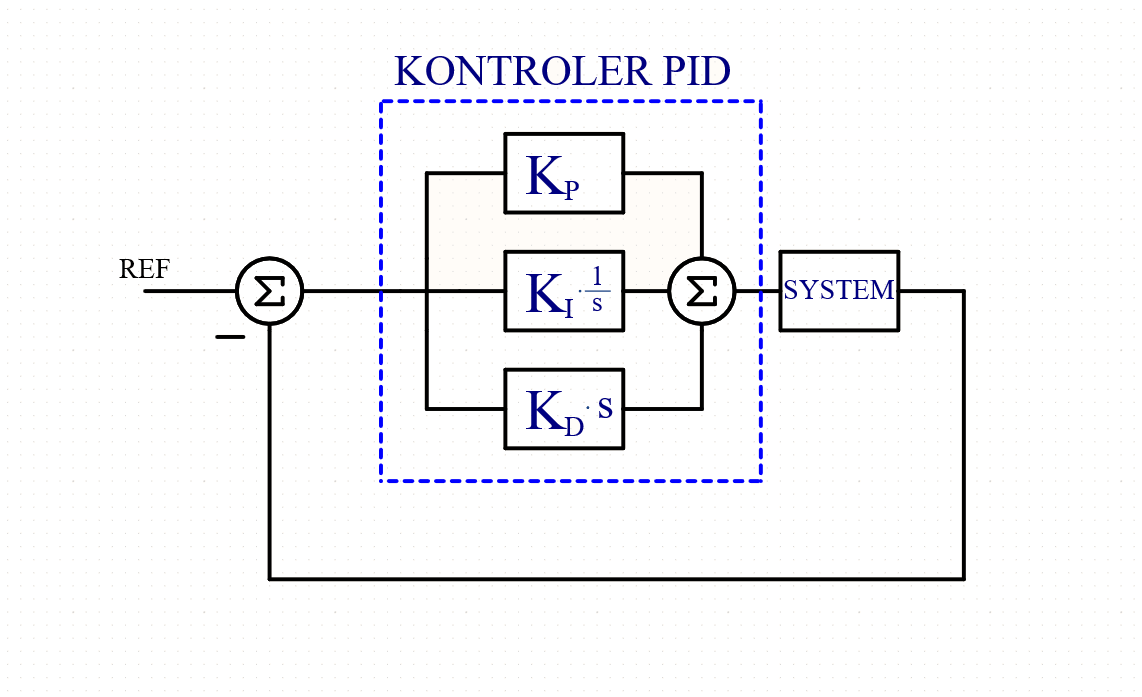
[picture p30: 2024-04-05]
images/drawing/PID.png

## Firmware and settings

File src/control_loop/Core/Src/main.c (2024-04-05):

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
/* Includes ------------------------------------------------------------------*/
#include "main.h"

/* USER CODE BEGIN Includes */
#include "PI.h"
/* USER CODE END Includes */

/* USER CODE BEGIN PTD */

/* HRTIM typedefs */
#define HRTIM_INPUT_CLOCK		((uint64_t)168000000)

#define _100kHz_PERIOD			((uint16_t)((HRTIM_INPUT_CLOCK * 32) / 100000))
#define _200kHz_PERIOD			((uint16_t)((HRTIM_INPUT_CLOCK * 32) / 200000))
#define _300kHz_PERIOD			((uint16_t)((HRTIM_INPUT_CLOCK * 32) / 300000))

#define _OPERATING_FREQ			_100kHz_PERIOD

#define VDDA					((uint16_t)3300)
#define DESIRED_VOLTAGE			((uint16_t)12000)

#define BUCK_THRSH				5000
#define MIXED_THRSH				((uint16_t)((DESIRED_VOLTAGE * 65 ) / 75))
#define BOOST_THRSH				((uint16_t)((DESIRED_VOLTAGE * 85 ) / 75))
#define OVERVOLTAGE				26000


/* USER CODE END PTD */

/* USER CODE BEGIN PD */
enum state
{
	BUCK = 1,
	BOOST = 2,
	BUCKBOOST = 3,
	DE_ENERGIZE = 4,
};
/* USER CODE END PD */

ADC_HandleTypeDef hadc1;
ADC_HandleTypeDef hadc2;
ADC_HandleTypeDef hadc4;
DMA_HandleTypeDef hdma_adc1;
DMA_HandleTypeDef hdma_adc2;
DMA_HandleTypeDef hdma_adc4;

HRTIM_HandleTypeDef hhrtim1;

void SystemClock_Config(void);
static void MX_GPIO_Init(void);
static void MX_DMA_Init(void);
static void MX_ADC1_Init(void);
static void MX_HRTIM1_Init(void);
static void MX_ADC2_Init(void);
static void MX_ADC4_Init(void);
/* USER CODE BEGIN PFP */
static void HRTIM_MultiplePWM(void);
/* USER CODE END PFP */

/**
  * @brief  The application entry point.
  * @retval int
  */
int main(void)
{
  /* USER CODE BEGIN 1 */

  // location for the adc conversion results
  volatile uint16_t adc1[2], adc2[2], adc4;

  // processed results
  uint16_t input_voltage, input_current,
  	  	   output_voltage, output_current,
		   choke_current;

  // PI controllers
  PIController PI_Outer_Buck, PI_Inner_Buck;
  PIController PI_Outer_Boost, PI_Inner_Boost;
  PIController PI_Outer_BB, PI_Inner_BB;

  // PI controller gains
  float BUCK_OUTER_KP = 0;
  float BUCK_OUTER_KI = 0;
  float BUCK_INNER_KP = 0;
  float BUCK_INNER_KI = 0;

  float BOOST_OUTER_KP = 0;
  float BOOST_OUTER_KI = 0;
  float BOOST_INNER_KP = 0;
  float BOOST_INNER_KI = 0;

  float BB_OUTER_KP = 0;
  float BB_OUTER_KI = 0;
  float BB_INNER_KP = 0;
  float BB_INNER_KI = 0;

  // enum for switch case
  enum state Converter_state;

  /* USER CODE END 1 */

  /* MCU Configuration--------------------------------------------------------*/

  /* Reset of all peripherals, Initializes the Flash interface and the Systick. */
  HAL_Init();

  /* Configure the system clock */
  SystemClock_Config();

  /* Initialize all configured peripherals */
  MX_GPIO_Init();
  MX_DMA_Init();
  MX_ADC1_Init();
  MX_HRTIM1_Init();
  MX_ADC2_Init();
  MX_ADC4_Init();
  /* USER CODE BEGIN 2 */

  // Mutiple PWM init
  HRTIM_MultiplePWM();

  //HRTIM start-up
  HAL_HRTIM_WaveformOutputStart(&hhrtim1, HRTIM_OUTPUT_TA1 | HRTIM_OUTPUT_TA2);
  HAL_HRTIM_WaveformOutputStart(&hhrtim1, HRTIM_OUTPUT_TB1 | HRTIM_OUTPUT_TB2);

  //Start counters
  HAL_HRTIM_WaveformCounterStart(&hhrtim1, HRTIM_TIMERID_TIMER_A);
  HAL_HRTIM_WaveformCounterStart(&hhrtim1, HRTIM_TIMERID_TIMER_B);

  // PI controllers init
  PIController_Init(PI_Outer_Buck, BUCK_OUTER_KP, BUCK_OUTER_KI);
  PIController_Init(PI_Inner_Buck, BUCK_INNER_KP, BUCK_INNER_KI);

  PIController_Init(PI_Outer_Boost, BOOST_OUTER_KP, BOOST_OUTER_KI);
  PIController_Init(PI_Inner_Boost, BOOST_INNER_KP, BOOST_INNER_KI);

  PIController_Init(PI_Outer_BB, BB_OUTER_KP, BB_OUTER_KI);
  PIController_Init(PI_Inner_BB, BB_INNER_KP, BB_INNER_KI);

  /* USER CODE END 2 */

  /* Infinite loop */
  /* USER CODE BEGIN WHILE */
  while (1)
  {
    /* USER CODE END WHILE */

    /* USER CODE BEGIN 3 */

	  // Input and output voltage, current measurements
	  HAL_ADC_Start_DMA(&hadc1, (uint32_t*)adc1, 2);
	  HAL_ADC_Start_DMA(&hadc2, (uint32_t*)adc2, 2);
	  HAL_ADC_Start_DMA(&hadc4, (uint16_t*)adc4, 1);

	  // Voltage bridge conversion is 120.05  	(16.5k / 1M + 1M + 16.5k), values in mV
	  // Shunt current conversion is 30.49		(1/800u * 41), values in mA

	  adc1[0] = adc1[0] * VDDA / 0xFFF;
	  adc1[1] = adc1[1] * VDDA / 0xFFF;
	  adc2[0] = adc2[0] * VDDA / 0xFFF;
	  adc2[1] = adc2[1] * VDDA / 0xFFF;
	  adc4    = adc4    * VDDA / 0xFFF;

	  input_voltage = (12005 * adc1[0]) / 100;
	  input_current = (3049 * adc1[1]) / 100;
	  output_voltage = (12005 * adc2[1]) / 100;
	  output_current = (3049 * adc2[0]) / 100;
	  choke_current = adc4;

	  if((input_voltage > BUCK_THRSH) && (input_voltage < MIXED_THRSH))  	  Converter_state = BUCK;
	  else if((input_voltage > MIXED_THRSH) && (input_voltage < BOOST_THRSH)) Converter_state = BUCKBOOST;
	  else if((input_voltage > BOOST_THRSH) && (input_voltage < OVERVOLTAGE)) Converter_state = BOOST;
	  else if(input_voltage > OVERVOLTAGE) 									  Converter_state = DE_ENERGIZE;

	  switch(Converter_state)
	  {

	  float pi_outer, pi_inner;
	  uint32_t newDC;
	  HRTIM_CompareCfgTypeDef compare_config;

	  case BUCK: // TIMER A - ON, TIMER B - OFF

		  // Set Duty Cycle as 0, TIMER B = 0 (Q3 open), ~B (Q4 shorted)
		  compare_config.CompareValue = 0;
		  HAL_HRTIM_WaveformCompareConfig(&hhrtim1, HRTIM_TIMERID_TIMER_B, HRTIM_COMPAREUNIT_1, &compare_config);

		  // calculate outer and inner PI controllers responses
		  pi_outer = PIController_Update(&PI_Outer_Buck, DESIRED_VOLTAGE, output_voltage);
		  pi_inner = PIController_Update(&PI_Inner_Buck, pi_outer, output_current);

		  // update duty cycle
		  newDC = (HRTIM_INPUT_CLOCK / _OPERATING_FREQ) * pi_inner;
		  compare_config.CompareValue = newDC;
		  HAL_HRTIM_WaveformCompareConfig(&hhrtim1, HRTIM_TIMERID_TIMER_A, HRTIM_COMPAREUNIT_1, &compare_config);

		  break;

	  case BOOST: // TIMER A - OFF, TIMER B - ON

		  // Set Duty Cycle as 1, TIMER A = 1 (Q1 shorted), ~A (Q2 open)
		  compare_config.CompareValue = 0xffff;
		  HAL_HRTIM_WaveformCompareConfig(&hhrtim1, HRTIM_TIMERID_TIMER_A, HRTIM_COMPAREUNIT_1, &compare_config);

		  // calculate outer and inner PI controllers responses
		  pi_outer = PIController_Update(&PI_Outer_Boost, DESIRED_VOLTAGE, output_voltage);
		  pi_inner = PIController_Update(&PI_Inner_Boost, pi_outer, output_current);

		  // update duty cycle
		  newDC = (HRTIM_INPUT_CLOCK / _OPERATING_FREQ) * pi_inner;
		  compare_config.CompareValue = newDC;
		  HAL_HRTIM_WaveformCompareConfig(&hhrtim1, HRTIM_TIMERID_TIMER_B, HRTIM_COMPAREUNIT_1, &compare_config);

		  break;

	  case BUCKBOOST: // TIMER A - ON (fixed duty cycle) , TIMER B - ON

		  // Set Duty Cycle as 0.75
		  compare_config.CompareValue = (HRTIM_INPUT_CLOCK / _OPERATING_FREQ) * 3 / 4;
		  HAL_HRTIM_WaveformCompareConfig(&hhrtim1, HRTIM_TIMERID_TIMER_A, HRTIM_COMPAREUNIT_1, &compare_config);

		  // calculate outer and inner PI controllers responses
		  pi_outer = PIController_Update(&PI_Outer_BB, DESIRED_VOLTAGE, output_voltage);
		  pi_inner = PIController_Update(&PI_Inner_BB, pi_outer, output_current);

		  // update duty cycle
		  newDC = (HRTIM_INPUT_CLOCK / _OPERATING_FREQ) * pi_inner;
		  compare_config.CompareValue = newDC;
		  HAL_HRTIM_WaveformCompareConfig(&hhrtim1, HRTIM_TIMERID_TIMER_B, HRTIM_COMPAREUNIT_1, &compare_config);
		  break;

	  case DE_ENERGIZE: // TIMER A - OFF (Q1 open, Q2 shorted), TIMER B - OFF (Q3 shorted, Q4 open)

		  // Set Duty Cycle as 0, TIMER A
		  compare_config.CompareValue = 0;
 		  HAL_HRTIM_WaveformCompareConfig(&hhrtim1, HRTIM_TIMERID_TIMER_A, HRTIM_COMPAREUNIT_1, &compare_config);

 		 // Set Duty Cycle as 1, TIMER B
 		 compare_config.CompareValue = 1;
 		 HAL_HRTIM_WaveformCompareConfig(&hhrtim1, HRTIM_TIMERID_TIMER_B, HRTIM_COMPAREUNIT_1, &compare_config);

		  break;

	  default:

		  break;

	  }
  }
  /* USER CODE END 3 */
}

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
/* USER CODE BEGIN 4 */

static void HRTIM_MultiplePWM(void)
{
	HRTIM_TimeBaseCfgTypeDef timebase_config;
	HRTIM_TimerCfgTypeDef timer_config;
	HRTIM_OutputCfgTypeDef output_config_TAx;
	HRTIM_OutputCfgTypeDef output_config_TBx;
	HRTIM_CompareCfgTypeDef compare_config;
	HRTIM_DeadTimeCfgTypeDef deadtime_config;


	/* HRTIM Global init */
	hhrtim1.Instance = HRTIM1;
	hhrtim1.Init.HRTIMInterruptResquests = HRTIM_IT_NONE;
	hhrtim1.Init.SyncOptions = HRTIM_SYNCOPTION_NONE;

	// HR Timer init
	HAL_HRTIM_Init(&hhrtim1);
	// DLL calibration, set period to 14us
	HAL_HRTIM_DLLCalibrationStart(&hhrtim1, HRTIM_CALIBRATIONRATE_1);
	// Wait calibration completion
	if (HAL_HRTIM_PollForDLLCalibration(&hhrtim1, 100) != HAL_OK)
	{
		Error_Handler(); /* if DLL or clock is not correctly set */
	}


	/* TIMERA init, TIMERA config */
	timebase_config.Period = _OPERATING_FREQ;
	timebase_config.RepetitionCounter = 0;
	timebase_config.PrescalerRatio = HRTIM_PRESCALERRATIO_MUL32;
	timebase_config.Mode = HRTIM_MODE_CONTINUOUS;
	HAL_HRTIM_TimeBaseConfig(&hhrtim1, HRTIM_TIMERINDEX_TIMER_A, &timebase_config);

	timer_config.DMARequests = HRTIM_TIM_DMA_NONE;
	timer_config.HalfModeEnable = HRTIM_HALFMODE_DISABLED;
	timer_config.StartOnSync = HRTIM_SYNCSTART_DISABLED;
	timer_config.ResetOnSync = HRTIM_SYNCRESET_DISABLED;
	timer_config.DACSynchro = HRTIM_DACSYNC_NONE;
	timer_config.PreloadEnable = HRTIM_PRELOAD_ENABLED;
	timer_config.UpdateGating = HRTIM_UPDATEGATING_INDEPENDENT;
	timer_config.BurstMode = HRTIM_TIMERBURSTMODE_MAINTAINCLOCK;
	timer_config.RepetitionUpdate = HRTIM_UPDATEONREPETITION_ENABLED;
	timer_config.ResetUpdate = HRTIM_TIMUPDATEONRESET_DISABLED;
	timer_config.InterruptRequests = HRTIM_TIM_IT_NONE;
	timer_config.PushPull = HRTIM_TIMPUSHPULLMODE_DISABLED;
	timer_config.FaultEnable = HRTIM_TIMFAULTENABLE_NONE;
	timer_config.FaultLock = HRTIM_TIMFAULTLOCK_READWRITE;
	timer_config.DeadTimeInsertion = HRTIM_TIMDEADTIMEINSERTION_DISABLED;
	timer_config.DelayedProtectionMode = HRTIM_TIMER_A_B_C_DELAYEDPROTECTION_DISABLED;
	timer_config.UpdateTrigger= HRTIM_TIMUPDATETRIGGER_NONE;
	timer_config.ResetTrigger = HRTIM_TIMRESETTRIGGER_NONE;
	HAL_HRTIM_WaveformTimerConfig(&hhrtim1, HRTIM_TIMERINDEX_TIMER_A,&timer_config);

	deadtime_config.Prescaler = HRTIM_TIMDEADTIME_PRESCALERRATIO_MUL8;
	deadtime_config.RisingValue = 0x000;
	deadtime_config.RisingSign = HRTIM_TIMDEADTIME_RISINGSIGN_POSITIVE;
	deadtime_config.RisingLock = HRTIM_TIMDEADTIME_RISINGLOCK_WRITE;
	deadtime_config.RisingSignLock = HRTIM_TIMDEADTIME_RISINGSIGNLOCK_WRITE;
	deadtime_config.FallingValue = 0x000;
	deadtime_config.FallingSign = HRTIM_TIMDEADTIME_FALLINGSIGN_POSITIVE;
	deadtime_config.FallingLock = HRTIM_TIMDEADTIME_FALLINGLOCK_WRITE;
	deadtime_config.FallingSignLock = HRTIM_TIMDEADTIME_FALLINGSIGNLOCK_WRITE;
	HAL_HRTIM_DeadTimeConfig(&hhrtim1, HRTIM_TIMERINDEX_TIMER_A, &deadtime_config);

	/* TA1 waveform description */
	output_config_TAx.Polarity = HRTIM_OUTPUTPOLARITY_HIGH;
	output_config_TAx.SetSource = HRTIM_OUTPUTSET_TIMPER;
	output_config_TAx.ResetSource  = HRTIM_OUTPUTRESET_TIMCMP1;
	output_config_TAx.IdleMode = HRTIM_OUTPUTIDLEMODE_NONE;
	output_config_TAx.IdleLevel = HRTIM_OUTPUTIDLELEVEL_INACTIVE;
	output_config_TAx.FaultLevel = HRTIM_OUTPUTFAULTLEVEL_NONE;
	output_config_TAx.ChopperModeEnable = HRTIM_OUTPUTCHOPPERMODE_DISABLED;
	output_config_TAx.BurstModeEntryDelayed = HRTIM_OUTPUTBURSTMODEENTRY_REGULAR;
	HAL_HRTIM_WaveformOutputConfig(&hhrtim1, HRTIM_TIMERINDEX_TIMER_A, HRTIM_OUTPUT_TA1, &output_config_TAx);

	/* TA2 waveform description */
	output_config_TAx.SetSource = HRTIM_OUTPUTSET_NONE;
	output_config_TAx.ResetSource  = HRTIM_OUTPUTRESET_NONE;
	HAL_HRTIM_WaveformOutputConfig(&hhrtim1, HRTIM_TIMERINDEX_TIMER_A, HRTIM_OUTPUT_TA2, &output_config_TAx);

	/* TIMERA Duty Cycles */
	compare_config.CompareValue = _OPERATING_FREQ/2;
	HAL_HRTIM_WaveformCompareConfig(&hhrtim1, HRTIM_TIMERINDEX_TIMER_A, HRTIM_COMPAREUNIT_1, &compare_config);

	compare_config.AutoDelayedMode = HRTIM_AUTODELAYEDMODE_REGULAR;
	compare_config.AutoDelayedTimeout = 0;
	compare_config.CompareValue = _OPERATING_FREQ/2;
	HAL_HRTIM_WaveformCompareConfig(&hhrtim1, HRTIM_TIMERINDEX_TIMER_A, HRTIM_COMPAREUNIT_2, &compare_config);

	/* TIMERD init */
	timebase_config.Period = _OPERATING_FREQ;
	timebase_config.RepetitionCounter = 0;
	timebase_config.PrescalerRatio = HRTIM_PRESCALERRATIO_MUL32;
	timebase_config.Mode = HRTIM_MODE_CONTINUOUS;
	HAL_HRTIM_TimeBaseConfig(&hhrtim1, HRTIM_TIMERINDEX_TIMER_B, &timebase_config);

	timer_config.DMARequests = HRTIM_TIM_DMA_NONE;
	timer_config.HalfModeEnable = HRTIM_HALFMODE_DISABLED;
	timer_config.StartOnSync = HRTIM_SYNCSTART_DISABLED;
	timer_config.ResetOnSync = HRTIM_SYNCRESET_DISABLED;
	timer_config.DACSynchro = HRTIM_DACSYNC_NONE;
	timer_config.PreloadEnable = HRTIM_PRELOAD_ENABLED;
	timer_config.UpdateGating = HRTIM_UPDATEGATING_INDEPENDENT;
	timer_config.BurstMode = HRTIM_TIMERBURSTMODE_MAINTAINCLOCK;
	timer_config.RepetitionUpdate = HRTIM_UPDATEONREPETITION_ENABLED;
	timer_config.ResetUpdate = HRTIM_TIMUPDATEONRESET_DISABLED;
	timer_config.InterruptRequests = HRTIM_TIM_IT_NONE;
	timer_config.PushPull = HRTIM_TIMPUSHPULLMODE_DISABLED;
	timer_config.FaultEnable = HRTIM_TIMFAULTENABLE_NONE;
	timer_config.FaultLock = HRTIM_TIMFAULTLOCK_READWRITE;
	timer_config.DeadTimeInsertion = HRTIM_TIMDEADTIMEINSERTION_DISABLED;
	timer_config.DelayedProtectionMode = HRTIM_TIMER_A_B_C_DELAYEDPROTECTION_DISABLED;
	timer_config.UpdateTrigger= HRTIM_TIMUPDATETRIGGER_NONE;
	timer_config.ResetTrigger = HRTIM_TIMRESETTRIGGER_NONE;
	HAL_HRTIM_WaveformTimerConfig(&hhrtim1, HRTIM_TIMERINDEX_TIMER_B,&timer_config);

	deadtime_config.Prescaler = HRTIM_TIMDEADTIME_PRESCALERRATIO_MUL8;
	deadtime_config.RisingValue = 0x000;
	deadtime_config.RisingSign = HRTIM_TIMDEADTIME_RISINGSIGN_POSITIVE;
	deadtime_config.RisingLock = HRTIM_TIMDEADTIME_RISINGLOCK_WRITE;
	deadtime_config.RisingSignLock = HRTIM_TIMDEADTIME_RISINGSIGNLOCK_WRITE;
	deadtime_config.FallingValue = 0x000;
	deadtime_config.FallingSign = HRTIM_TIMDEADTIME_FALLINGSIGN_POSITIVE;
	deadtime_config.FallingLock = HRTIM_TIMDEADTIME_FALLINGLOCK_WRITE;
	deadtime_config.FallingSignLock = HRTIM_TIMDEADTIME_FALLINGSIGNLOCK_WRITE;
	HAL_HRTIM_DeadTimeConfig(&hhrtim1, HRTIM_TIMERINDEX_TIMER_B, &deadtime_config);

	/* TD1 waveform description */
	output_config_TBx.Polarity = HRTIM_OUTPUTPOLARITY_HIGH;
	output_config_TBx.SetSource = HRTIM_OUTPUTSET_TIMPER;
	output_config_TBx.ResetSource  = HRTIM_OUTPUTRESET_TIMCMP1;
	output_config_TBx.IdleMode = HRTIM_OUTPUTIDLEMODE_NONE;
	output_config_TBx.IdleLevel = HRTIM_OUTPUTIDLELEVEL_INACTIVE;
	output_config_TBx.FaultLevel = HRTIM_OUTPUTFAULTLEVEL_NONE;
	output_config_TBx.ChopperModeEnable = HRTIM_OUTPUTCHOPPERMODE_DISABLED;
	output_config_TBx.BurstModeEntryDelayed = HRTIM_OUTPUTBURSTMODEENTRY_REGULAR;
	HAL_HRTIM_WaveformOutputConfig(&hhrtim1, HRTIM_TIMERINDEX_TIMER_B, HRTIM_OUTPUT_TB1, &output_config_TBx);

	/* TD2 waveform description */
	output_config_TBx.SetSource = HRTIM_OUTPUTSET_TIMCMP2;     //HRTIM_OUTPUTSET_NONE;
	output_config_TBx.ResetSource  = HRTIM_OUTPUTRESET_TIMPER; //HRTIM_OUTPUTRESET_NONE;
	HAL_HRTIM_WaveformOutputConfig(&hhrtim1, HRTIM_TIMERINDEX_TIMER_B, HRTIM_OUTPUT_TB2, &output_config_TBx);
}



/* USER CODE END 4 */
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


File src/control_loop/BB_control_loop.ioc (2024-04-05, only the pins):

Mcu.UserName=STM32G474RETx
PA0.Signal=ADC1_IN1
PA1.Signal=ADC1_IN2
PA10.Signal=HRTIM1_CHB1
PA11.Signal=HRTIM1_CHB2
PA13.GPIO_Label=T_SWDIO
PA13.Signal=SYS_JTMS-SWDIO
PA14.GPIO_Label=T_SWCLK
PA14.Signal=SYS_JTCK-SWCLK
PA2.GPIO_Label=LPUART1_TX [STLINKV3E_VCP_RX]
PA2.Signal=LPUART1_TX
PA3.GPIO_Label=LPUART1_RX [STLINKV3E_VCP_TX]
PA3.Signal=LPUART1_RX
PA5.GPIO_Label=LD2 [green led]
PA5.Signal=GPIO_Output
PA7.Signal=ADC2_IN4
PA8.Signal=HRTIM1_CHA1
PA9.Signal=HRTIM1_CHA2
PB11.Signal=ADC2_IN14
PB12.Signal=ADC4_IN3
PB14.Signal=ADC4_IN4
PB15.Signal=ADC2_IN15
PB3.GPIO_Label=T_SWO
PB3.Signal=SYS_JTDO-SWO
PC1.Signal=ADC1_IN7
PC13.GPIO_Label=B1 [blue push button]
PC13.Signal=GPXTI13
PC14-OSC32_IN.Signal=RCC_OSC32_IN
PC15-OSC32_OUT.Signal=RCC_OSC32_OUT
PC2.Signal=ADC1_IN8
PC4.Signal=ADC2_IN5
PF0-OSC_IN.Signal=RCC_OSC_IN
PF1-OSC_OUT.Signal=RCC_OSC_OUT

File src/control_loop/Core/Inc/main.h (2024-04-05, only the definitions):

#define B1_Pin GPIO_PIN_13
#define B1_GPIO_Port GPIOC
#define B1_EXTI_IRQn EXTI15_10_IRQn
#define LPUART1_TX_Pin GPIO_PIN_2
#define LPUART1_TX_GPIO_Port GPIOA
#define LPUART1_RX_Pin GPIO_PIN_3
#define LPUART1_RX_GPIO_Port GPIOA
#define LD2_Pin GPIO_PIN_5
#define LD2_GPIO_Port GPIOA
#define T_SWDIO_Pin GPIO_PIN_13
#define T_SWDIO_GPIO_Port GPIOA
#define T_SWCLK_Pin GPIO_PIN_14
#define T_SWCLK_GPIO_Port GPIOA
#define T_SWO_Pin GPIO_PIN_3
#define T_SWO_GPIO_Port GPIOB

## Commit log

2024-04-05 Thesis upload
    [Boost_eff.csv, Buck-Boost_eff.csv, Buck_eff.csv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]
2024-04-05 deletiun of unnecessary files
    [Drawing.SchDoc, schematic_library.SchLib]

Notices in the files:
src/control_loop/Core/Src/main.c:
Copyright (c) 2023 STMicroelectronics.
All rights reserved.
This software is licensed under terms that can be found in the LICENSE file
